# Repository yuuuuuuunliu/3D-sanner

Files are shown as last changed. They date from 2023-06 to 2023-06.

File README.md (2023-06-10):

# Ultrasonic 3D Scanner

This guide outlines the development process of our ultrasonic 3D scanner. We will provide resources in this repository that can be used to reproduce the project, as well as data for evaluating the accuracy of the measurement results. The ultrasonic 3D scanner utilizes ultrasound ranging to scan real-world objects, capturing the coordinates of various points on their surfaces. By processing the collected data, the scanner generates a three-dimensional model of the object, enabling an accurate digital representation of the object's size and dimensions. This technology holds immense potential for various applications, including but not limited to artifact preservation, educational applications, and reverse engineering. Our project specifically focuses on constructing a low-cost 3D scanner, aiming to make this technology more accessible for everyday use. By providing an affordable solution, we aim to promote the widespread adoption of this technology in everyday life.

Access our project presentation through this link: 

https://docs.google.com/presentation/d/14-DhOLEjQ7N0TpDgxVi51gBwk0Xk7jdvzFTlWsp83JA/edit?usp=sharing

We hope you enjoy exploring this guide and find it helpful in creating your own 3D scanner.
 
## Table of Contents
* [Description](https://github.com/yuuuuuuunliu/3D-sanner#Description)
* [List of Components](https://github.com/yuuuuuuunliu/3D-sanner#List_of_Components)
* [Method](https://github.com/yuuuuuuunliu/3D-sanner#Method)
* [Construction](https://github.com/yuuuuuuunliu/3D-sanner#Construction)
* [Product Review](https://github.com/yuuuuuuunliu/3D-sanner#Product_Review)
* [Future Development](https://github.com/yuuuuuuunliu/3D-sanner#Future_Development)
* [Contributors](https://github.com/yuuuuuuunliu/3D-sanner#Contributors)
* [Acknowledgments](https://github.com/yuuuuuuunliu/3D-sanner#Acknowledgments)

## Description
The ultrasonic 3D scanning device consists of two main components: a fixed ultrasonic distance sensor and a rotatable lifting platform. The ultrasonic distance sensor utilizes the reflection of sound waves to determine the distances between its position and various points on an object. The lifting platform is powered by a stepper motor and is driven by gears and screws to rotate and elevate the object. As the platform rotates, the object passes through the ultrasonic distance sensor in a spiral path, and the coordinates of the object's points are recorded.

Subsequently, we process the collected data using MATLAB and extract the outer contour of the scanned object to generate a three-dimensional model. This is achieved through an interactive program that allows us to visualize the reconstructed 3D model based on the acquired data.

## List of Components
  * Ultrasonic Distance Sensor - HC-SR04
  * Arduino Nano 3.x
  * 4 Phase ULN2003 Stepper Motor Driver PCB
  * 28BYJ-48 - 5V Stepper Motor
  * Arduino Uno Mini LE - MCU 8-Bit Embedded Evaluation Board
  * Screw and nut
  * PCB Board
  * Jumper wires
  * 3D-printed parts

## Method
We use HC-SR04 as the ultrasound distance sensor component.
  
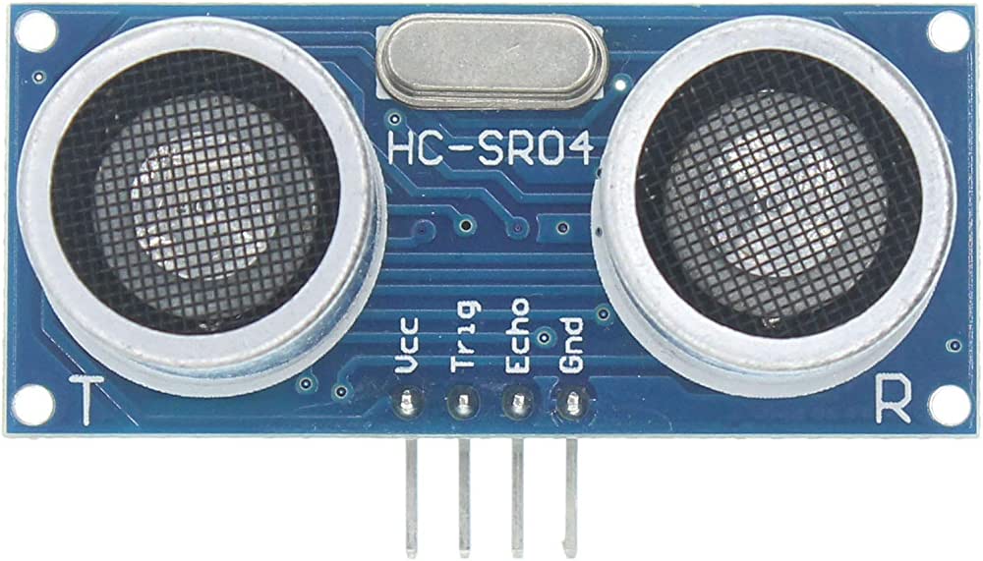
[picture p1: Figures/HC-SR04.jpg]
A picture of the distance sensor we used
  
  
The HC-SR04 module consists of four pins. The Vcc pin and GND pin are connected to the 5V and GND pins of the Arduino Nano, respectively. These pins serve as both power supply and logic level control (high/low). The Trig pin is an input pin of the HC-SR04 and is connected to the D3 pin of the Arduino Nano. The Echo pin is an output pin of the HC-SR04 and is connected to the D2 pin of the Arduino Nano. In fact, the Trig and Echo pins can be connected to any two digital I/O pins of the Arduino Nano. The HC-SR04 module consists of two piezoelectric transducers, one acting as a transmitter (marked with "T") and the other as a receiver (marked with "R"). 

To initiate a distance measurement with the HC-SR04 module, a voltage pulse is sent to the Trig pin. This voltage pulse is transformed into a sine wave by a local oscillator, and the resulting sine-shaped voltage signal is sent to the transmitter. The transmitter converts this voltage signal into a sound signal, emitting an 8-cycle sonic burst in the forward direction. Simultaneously, the receiver is set to a high state, and a timer starts counting. The emitted sonic burst travels through space and reflects when it encounters the nearest object. Upon receiving the reflected wave, the receiver changes to a low state, indicating the detection of the reflected signal, and the timer stops counting. 

The duration for which the receiver stays in a high state is equal to the time it takes for the sound to travel in space. Therefore, the distance between the sensor and the object can be calculated using the formula: d = (v * t) / 2, where t represents the measured time and v represents the speed of sound. The speed of sound is typically considered to be around 340 m/s, but it can vary depending on the medium and temperature conditions.

We aim to have three spatial dimensions for each data point to determine their coordinates in space accurately. Since the trajectory of the object moving in front of the sensor is spiral-shaped, expressing the coordinates in cylindrical coordinates would be the most convenient way. The actual measurement results include two dimensions - time (t) and distance (d). By introducing the angular velocity (ω) of the rotating disc and the vertical velocity (v), we can represent the angle (θ) between the point's position along the radial axis and the initial radial axis as a function of time (t), as well as the distance (z) between the point's position and the initial plane as a function of time (t). Introducing the distance (r_max) from the sensor to the vertical axis of the cylinder allows us to calculate the distance (s) between the measurement point and the vertical axis of the cylinder. Hence, we can determine the cylindrical coordinates (s, θ, z) of each point on the object's surface in a coordinate system with the initial plane as the xy-plane and the vertical axis of the cylinder as the z-axis. The specific formulas for the calculations are as follows:

$$s = r_{max} - d$$

$$\theta = \omega * t$$

$$z = v * t$$

Once we have marked all the points on the object's surface in space, our goal is to construct the outer surface of the object using these points. While we can easily visualize the outer surface, computers have numerous possibilities for constructing planes based on the given points. Therefore, we need to specify the desired planes. The instruction we provide to the computer is to connect points with adjacent θ and z values, and to fill all the quadrilaterals bounded by the connecting lines. This process allows us to construct the outer surface of the object. 

For the specific MATLAB graphing code, please refer to the following location, where I generate data for simulation purposes:https://github.com/yuuuuuuunliu/3D-sanner/blob/main/graph.mlx

The expected outcome is shown below:

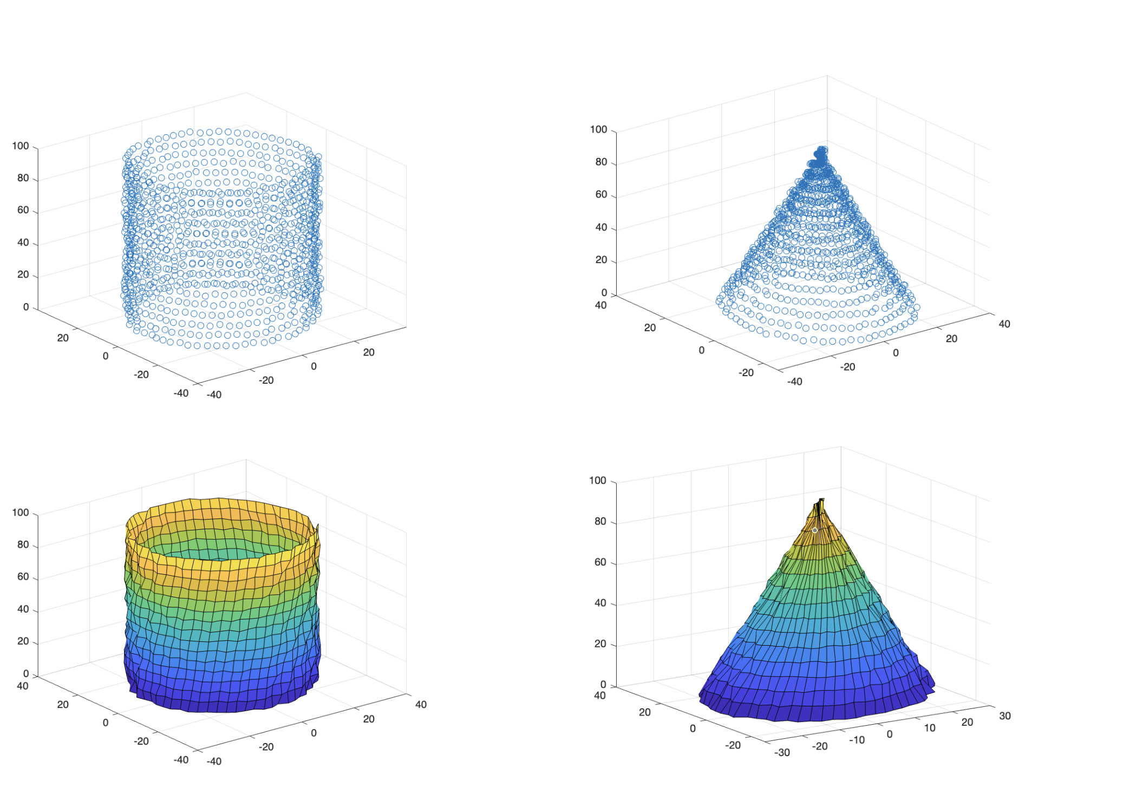
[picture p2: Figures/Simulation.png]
Outer surface of a cylinder and a cone using simulated data
  

In order to scan the 3D information of an object, we rotate the object and make it move upward. The sensor is fixed and gets information when the system is start to work. In this way, we just need to collect the information on time and distance from the sensor to the object. The location can be calculated from the time and velocity of the step motor. The step motor rotates one lap in 4 seconds. The plate rotates 1 lap using 10 seconds. In each lap, the object will raise 2 mm with the average speed with the plate. 

The rotating frame is motivated by a stepper motor with following circuit connection:

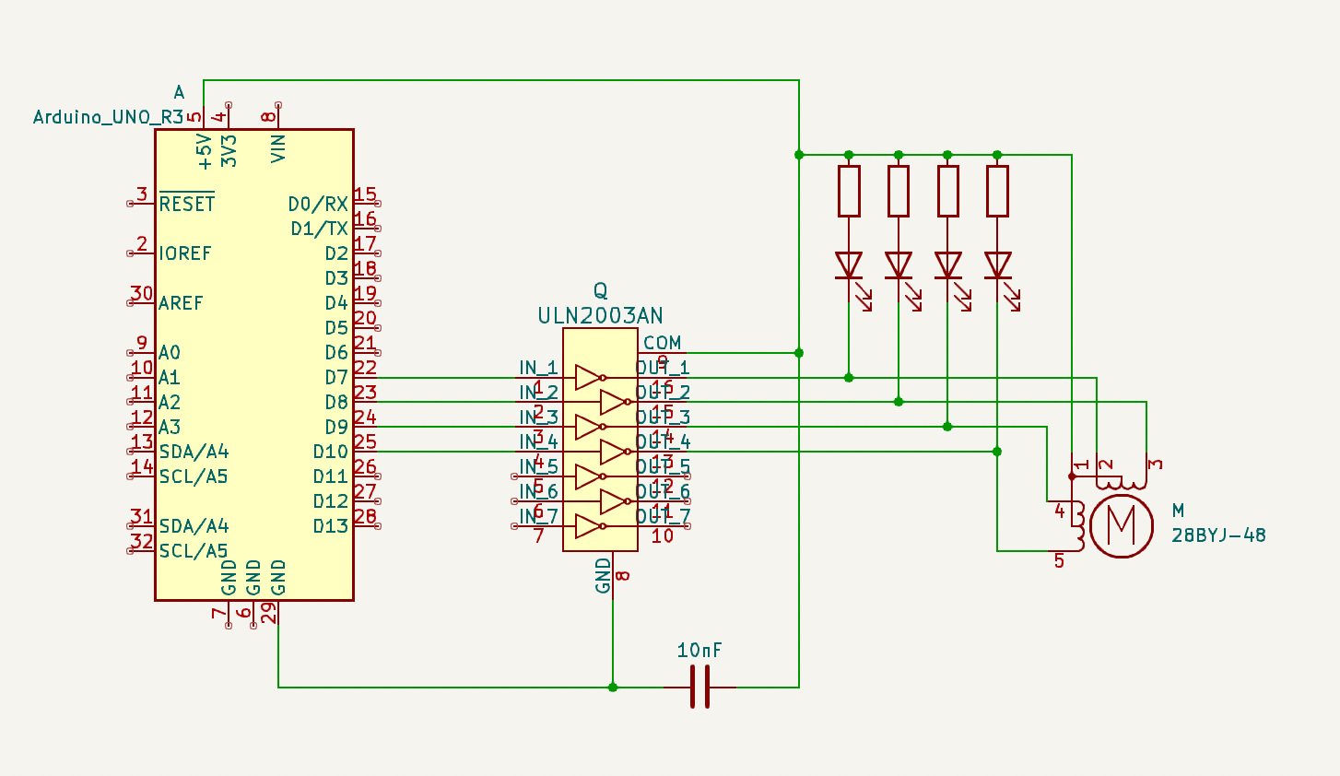
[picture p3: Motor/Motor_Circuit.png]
Circuit connection of stepper motor, driver, and Aduino
  

## Construction

Before scanning the object, we build up a frame to hold all components. For most of the components, we used 3D Modeling to create and then print them out with 3D printers. All of STL. Files can find in the folder of [Frame](https://github.com/yuuuuuuunliu/3D-sanner/tree/main/Frame). Some components have different versions, we did lots of improvements for every component. 

The plate will hold the object we are going to scan. The main frame is going to fix the nut and hold the whole system. It can replace by box instead of 3D printing components, because large 3D printing components take a long time, which may take up to several days. A strew is connect with the plate and the strew gear. Before assemble them, the nut and connection should install first. From the top to the bottom of the strew, the sequence should be plate, nut, connection, and strew gear. The step motor should connect to the middle whole of the connection. Then, install step motor gear onto it and check the connection between step motor gear and the strew gear. The connection is free to rotate with the strew. The frame should limit this rotation and make sure it can move up and downward with the strew. Other parts work for fix the sensor, they are flexible to do adjustments due to your different use. 

* [Different printers may print out components with different uncertainty. Some adjustments may be needed especially for the gears. If the gears have spinning conditions, enlarging the teeth of gears for 1mm is a good choice.] 

HC-SR04 has a range from 2cm to 4m. Experimental results have shown that the HC-SR04 distance sensor has a measurement standard deviation of less than 0.5mm. The difference between measured values and actual values is typically less than 2cm, with the majority of errors staying below 0.5cm. Therefore, we can consider the HC-SR04 to be a precise and accurate distance sensor. Additionally, due to its stable numeric uncertainty rather than percentage uncertainty, we can reduce errors by applying it to large objects. This improvement strategy will be further discussed in the future development section.

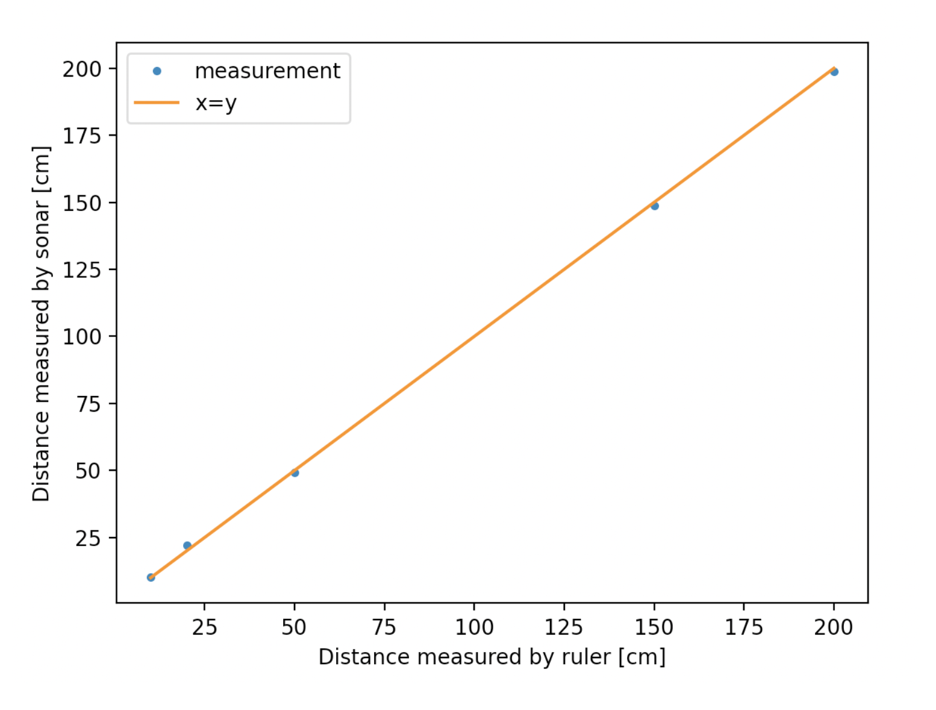
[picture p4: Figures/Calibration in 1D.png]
A plot of the sensor's measurements against the actual length
  

The distance sensor we utilize emits a conical wave with a raypath angle of 15 degrees. This angle allows the sensor to be sensitive to a wider area. However, in situations where high precision distance measurements are required, such high sensitivity can lead to unnecessary feedback. To mitigate this, we can place a rough absorbent block beneath the sensor. This block, with its rough surface, causes non-radial sound waves to undergo multiple reflections in a short period of time, dissipating a significant amount of energy and effectively absorbing unwanted reflected waves. 

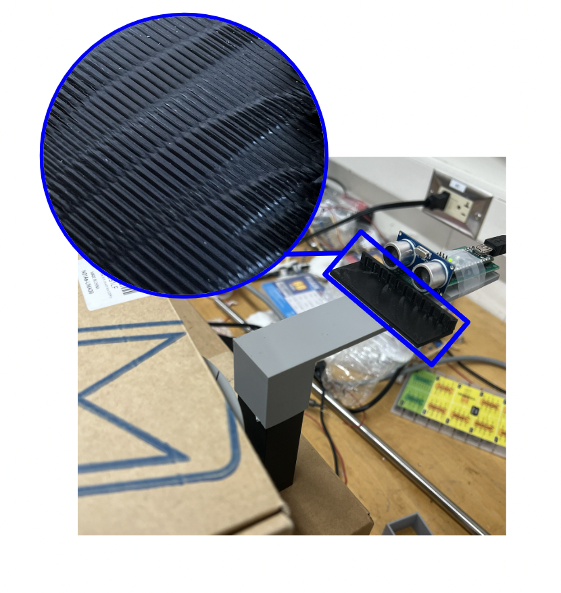
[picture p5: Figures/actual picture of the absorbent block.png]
A picture of the absorbent block and a close-up look of its surface
  

The figure below illustrates the results obtained when using the sensor to measure a stationary object (i.e., where the distance from the point to the origin, s, remains constant), and processing the data using MATLAB to generate a three-dimensional image in cylindrical coordinates. It is evident that the erroneous refracted points have been effectively eliminated through the use of the absorbent block.
 
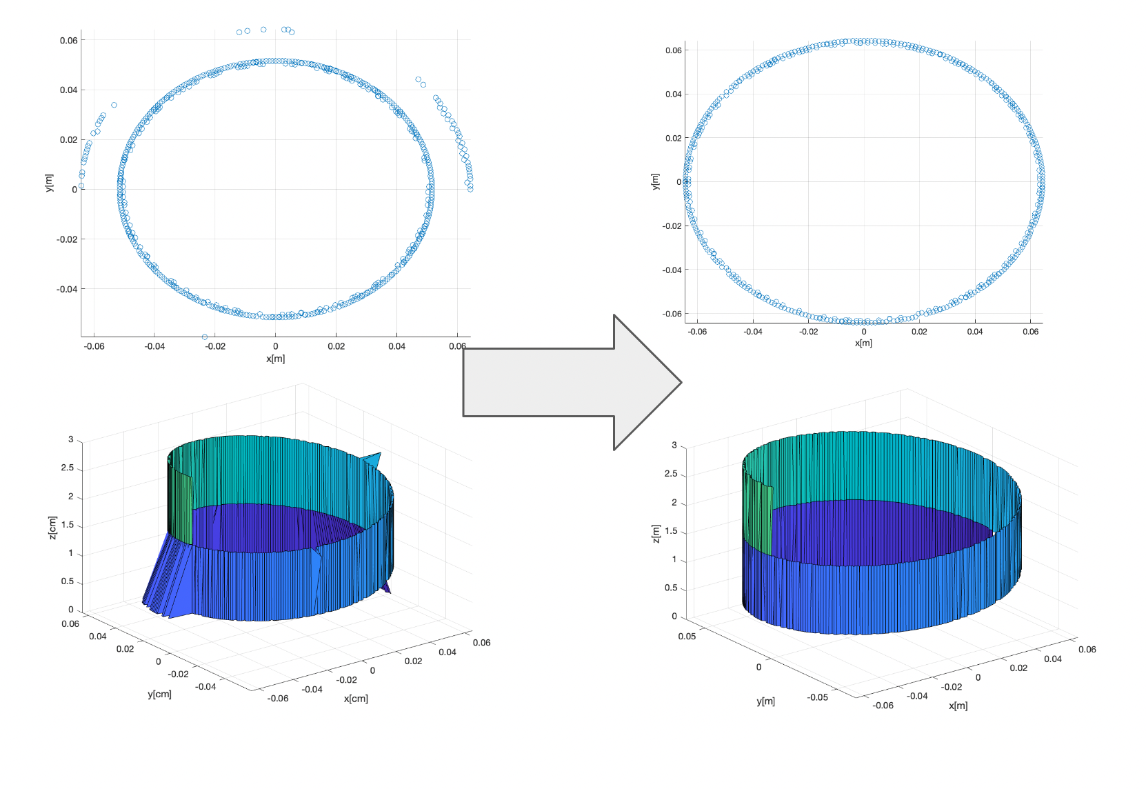
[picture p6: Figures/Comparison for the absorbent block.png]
Comparison of plots before and after using the absorbent block
  
  
We use the device to scan the surface of a cylindrical object. Ideally, the results obtained after the rotation of the turntable should be similar to the results obtained when the turntable is stationary, as the object exhibits cylindrical symmetry around the z-axis. However, in reality, the results obtained after the rotation of the turntable exhibit significant fluctuations. By observing the raw data and examining the scanned image of the object's outer surface based on the measurement results, we notice that the fluctuations in the raw data appear to be periodic. This observation is further supported by the presence of a wavy surface in the 3D representation. Therefore, we have decided to use the "smoothdata" function in MATLAB to remove these fluctuations.

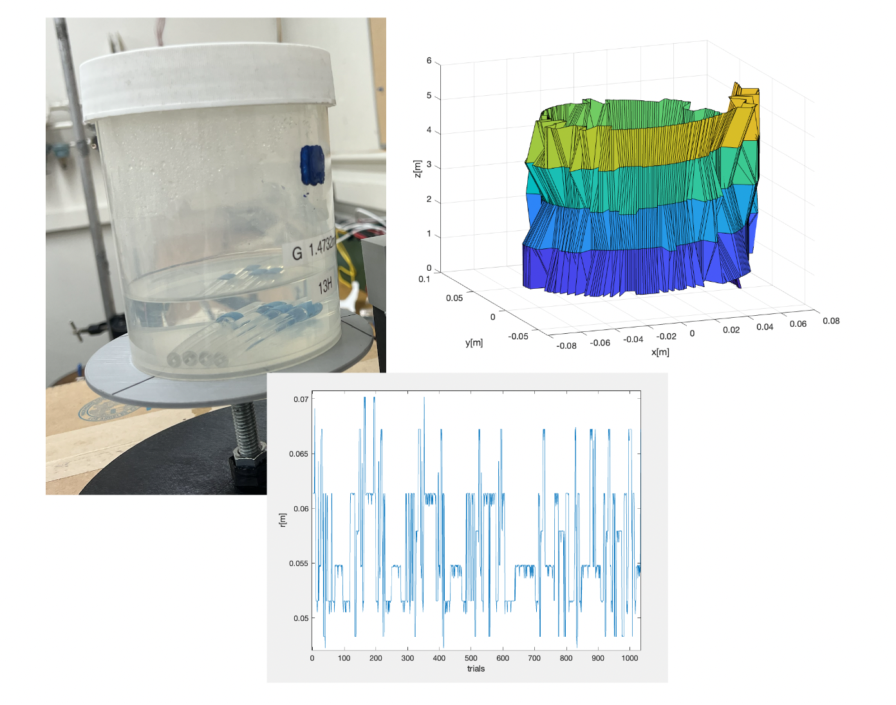
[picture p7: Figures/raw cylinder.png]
Pictures that showcase the cylindrical object, the raw data of r over multiple trials, and a 3D graph generated based on the measurements
  

The code we used is as follows:

```
smoothdData = smoothdata(r, "movmean", 50)
```

In this code, "r" represents the data to be processed, "movmean" denotes the data processing method, and "50" indicates the window size. The provided function creates a moving window with a size of 50 data. This window calculates the average value of all 50 data it contains and treats it as the smoothed data. Then, the window shifts by one value and the process is repeated. The window moves along the data while continuously calculating the average value until all the data is smoothed. Plotting the graph using the smoothed data reveals that a significant amount of noise has been removed. The resulting image exhibits a relatively smooth surface, which is what we desired.

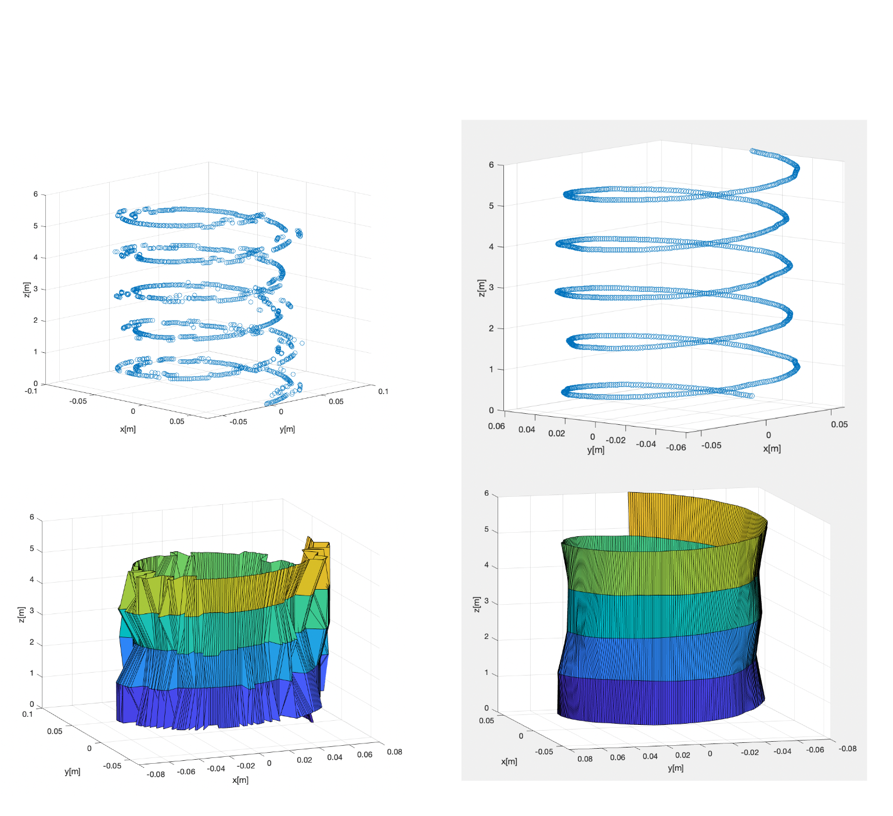
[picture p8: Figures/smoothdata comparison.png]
A comparison of the final 3D graphs between using the smoothdata() function and not using it
  

## Product Review

### Scanning two stacked cylinders with different radius

The arrangement of the scanned objects is illustrated in the following diagram:

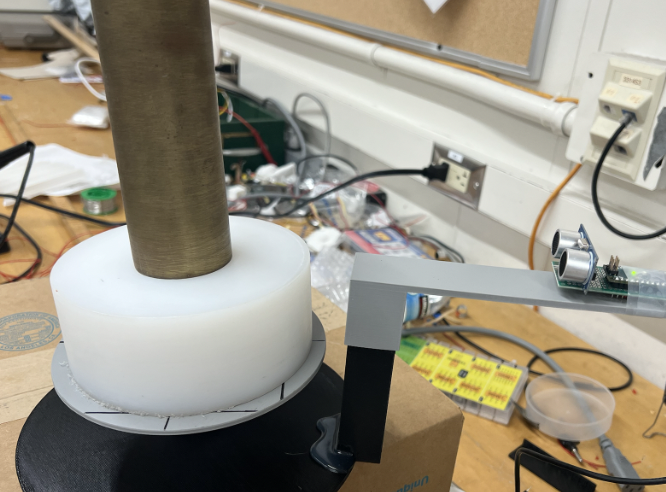
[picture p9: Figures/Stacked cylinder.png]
The arrangement of two stacked cylinders that will be scanned for review
  
 
The lower cylinder has a radius of approximately 6.5cm, while the upper cylinder has a radius of approximately 2.5cm. Both the raw data and smoothed data show a reduction in radius, which corresponds to our actual setup. 

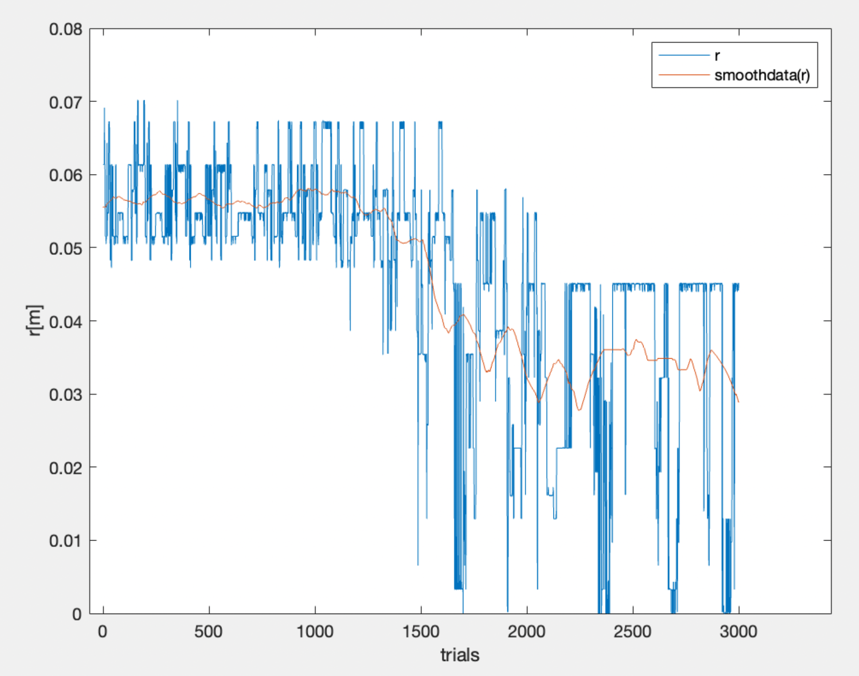
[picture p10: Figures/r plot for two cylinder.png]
The plot showing the variation of distance r over trial for both raw data and smoothed data
  

We then examine the processed 3D image. The image roughly depicts the outer contours of two cylinders with different radii. At the same time, we can approximately read the measured values of the two cylinder radii from the graph, which are approximately 3cm and 6cm. Comparing these values to the actual data, we find an error of approximately 0.5cm, which aligns with the expected deviation in the initial direct measurements of distance using the ultrasonic sensor. Therefore, we can conclude that the precision of our obtained results is close to the inherent precision limit of the HC-SR04 sensor. For the current setup, this is a satisfactory outcome. Indeed, it is noticeable that in the region where the two cylinders are joined, the graph does not exhibit sharp edges as we would expect in the real world. Instead, there is a curved and smooth transition between the surfaces of the cylinders. This result is attributed to the 15-degree raypath angle of the sound waves, as we discussed earlier, and the inclination of the platform. Possible solutions for this issue will be elaborated in detail in the future development section.

  The 3D surface graph generated by MATLAB as well as the distribution of measured data points in 3D space (top view)
  
However, the resulting image this time does not resemble a box in any way. Upon careful observation of the scanning process of the box and experimenting with different platform rotation speeds in Matlab, we have found that the failure in imaging the box is due to the instability of the platform rotation speed.

### Scanning a box

Then we proceed to scan the box as illustrated in the following image:

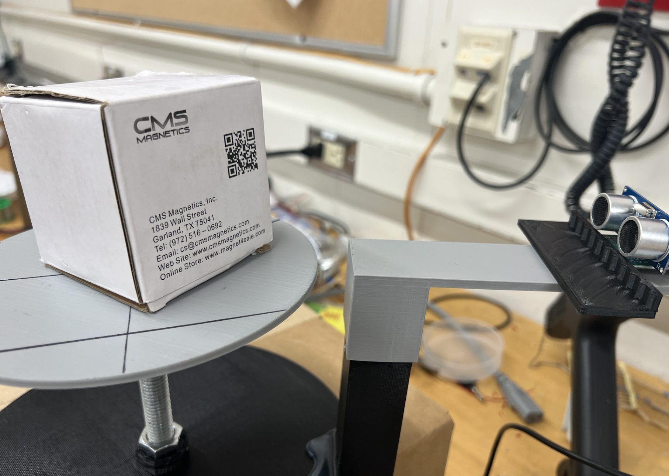
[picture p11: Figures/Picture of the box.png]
The picture of the box we will scan in this section
  
  
However, the resulting image this time does not resemble a box in any way. Upon careful observation of the scanning process of the box and experimenting with different platform rotation speeds in Matlab, we have found that the failure in imaging the box is due to the instability of the platform rotation speed. When processing the data in MATLAB to generate the 3D image, it assumes an ideal motion model for the platform based on a constant vertical speed and angular speed. However, during the actual measurement process, we observed that the platform's rotation speed is not stable. The time required for a point on the surface of the object to complete a full 2π rotation varies in each revolution. As a result, MATLAB can only ensure that the points on the same revolution as the set angular speed are in the right phase. However, MATLAB requires at least two revolutions of points to generate one complete surface. This discrepancy leads to the final generated result being distorted and skewed. We will provide a detailed explanation of the proposed solutions for this issue in the future development section.

  The 3D scan of the box in both scatter plot and surface plot versions

## Future Development
We have already mentioned some of the issues and unexpected results encountered in the previous discussion. In order to address these problems, we plan to upgrade the project in the future. Additionally, we will conduct corresponding experiments to investigate the causes of the unexpected results. Specific future measures that can be undertaken are outlined as follows:

### Upgrade of the rotating platform

At the current stage, the rotating platform exhibits the following issues: Firstly, the rotating disc is not perfectly horizontal, causing a precession in the coordinate system in which the object is located as perceived by the distance sensor. Secondly, there are certain issues with the gear size, resulting in improper engagement. The gears that rotate synchronously with the rotating disc often experience slipping and jamming, leading to an unstable rotational speed. Lastly, the device is built on a cardboard box, which has low density. This causes the entire setup to shake under the influence of the stepper motor driving and the inertia of object rotation, significantly affecting the final scanning results. This shaking may also be a potential cause of the periodic noise observed in the raw data we discussed earlier，although further measurement and analysis are required to confirm this hypothesis.
Adjustments on 3D printing can solve some problem. For example, adjust the size of plate and enlarge the teeth of gears can solve the first two problems. Also, this method can make the system works more stable as well, which can reduce some vibration. Also, the frame should be upgrade to all-3D-printed one. It may take a long time to print, but it is heavier and more stable. Additionally, create new 3D modeling of protection cover for the sensor may help to reduce noise. 

### Upgrade of the ultrasonic distance sensor

As mentioned earlier, the HC-SR04 sensor emits ultrasonic waves in the form of a cone with a vertex angle of 15 degrees. This characteristic introduces certain measurement errors and inaccuracies in capturing sharp edges of objects. We aim to narrow down the scanning range by utilizing phased array technology. Inspired by the video shared (https://www.youtube.com/watch?v=Evao3XUUAOY), we came up with the idea of employing a phased array approach to achieve this goal.By strategically spacing multiple wave sources and adjusting their phases, we can control the interference pattern of the emitted waves. This allows us to constructively interfere the waves along the desired path, forming a stronger sound ray, while causing destructive interference in other directions to minimize their impact on the main beam. We can build our own multi-wave source distance sensor to achieve a more focused detection beam. By using basic electronic components, we can design a distance sensor that provides analog signals instead of the digital output of the HC-SR04 module. By processing and analyzing the analog signals, we can extract information about multiple reflections, allowing us to obtain insights into the internal structure of objects.

### Upgrade of smoothdata() method

In the previous experiments, I chose a window size of 50 based on multiple trial runs. This particular window size was found to strike a balance between data accuracy and precision while avoiding potential trial-specific outcomes. However, upon realizing that the noise we want to eliminate is periodic, measuring the period of the noise will help us determine a more appropriate window size. Therefore, in the future, we will attempt to measure the periodicity of the noise and explore the relationship between window size, periodicity of the noise, and the accuracy and precision of the final results by scanning objects with different shapes and symmetries.

### Research on periodic noise

Ideally, when scanning a cylindrical object with a base radius of R, the results should be consistent whether the turntable is rotating or stationary because both measurement methods essentially involve continuously measuring R. However, in reality, we have observed that when the turntable is stationary, the measurement error generated by the ultrasonic sensor is negligible. However, when the turntable starts rotating, significant periodic errors occur in the measurement results from the ultrasonic sensor, which can significantly impact the quality of the imaging. Therefore, we have developed some initial hypotheses regarding the origin of this periodic error: it stems from the rotation of the turntable. We aim to investigate whether the periodicity of the error changes with variations in the rotational speed of the turntable. Through this experiment, we will have the opportunity to confirm the source of the error and conduct further research to pinpoint the underlying causes of the noise.

## Contributors

This project was undertaken as part of the PHYS 13CL course at UCSB.

We would like to extend our sincere appreciation to Professor Andrew Jayich and the teaching assistants, Robert Kwapisz and Eric Deck. Their unwavering support and guidance throughout these ten weeks have been invaluable to our project. We are also grateful to them for organizing enjoyable board game nights that helped alleviate our stress, and for feeding our restless souls with pizza and Fanta.

Furthermore, we would like to express our gratitude to thet group of Katelyn Saxen, Katya Osipova, and Eric Zhu for generously sharing their experiences and providing valuable insights when we encountered challenges during our progress.

Special thanks go to Raffi Shirinian for his assistance in utilizing the 3D printer and for lending us his personal hot glue gun, which greatly facilitated our project.

We would also like to thank Max Kolevski for his assistance in procuring the stepper motor and driver from ILG, which were instrumental to the success of our project.

Lastly, we want to acknowledge and thank Reuben Beeler for his thought-provoking questions during the presentation. His inquiries inspired us to reevaluate our criteria for evaluating the scan results.

## Acknowledgments
* [Datasheet of HC-SR04](https://cdn.sparkfun.com/datasheets/Sensors/Proximity/HCSR04.pdf)
* [Datasheet of 4 Phase ULN2003 Stepper Motor Driver PCB](https://www.electronicoscaldas.com/datasheet/ULN2003A-PCB.pdf)
* [Datasheet of 28BYJ-48 – 5V Stepper Motor](https://www.mouser.com/datasheet/2/758/stepd-01-data-sheet-1143075.pdf)
* [Control 28BYJ-48 Stepper Motor with ULN2003 Driver & Arduino](https://lastminuteengineers.com/28byj48-stepper-motor-arduino-tutorial/)
* [DIY Sonar Scanner Using Phased Array](https://www.youtube.com/watch?v=Evao3XUUAOY)

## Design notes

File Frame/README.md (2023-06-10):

## Frame
This component has two versions, it is mainly designed for holding and fixing all the needed components and parts for the project. Strew's nut should be fixed on it. 

## Gear
This is connnect to the step motor. It works to transmit force from step motor to the strew and then rotate the object. "gear, step motor v2" is the second version of it. The second version has longer teeth, which solve the problem of spinning between two gears. 

## Strew Gear
This is design to fix with the strew we bought. The step motor will transmit force through step motor gear to make the strew rotate. 

## Connection
This components is design to hold the step motor and connect strew with the step motor. This connection should move up or down with the strew and step motor as rotating, but it should not rotate with the strew. In this way, the step motor can generate the strew to move up and rotate. 

## Coverage Frame
This component is designed to hold our sensor. the rectangle part is use to connect with the frame. It is a seperate part from the frame because of the limited space for the 3D printer. 

## Rail Base
This is design for the 2-D experiment. It works with the step motor and generate the sensor to move in a straight line. 

## Plate
This object connects to the strew directly. It rotates with the strew and hold the object we are going to scan. 

### Attention
In order to connect different components will. I suggest to print the coverage frame with a 1mm-1.5mm larger width, the step motor gear with 1mm longer teeth. It is able to add more teeth for the strew gear. The original strew gear has 20 teeth which is 2.5 times teeth that the step motor gear has. The original one is more convenient for calculating the angular speed of plate.

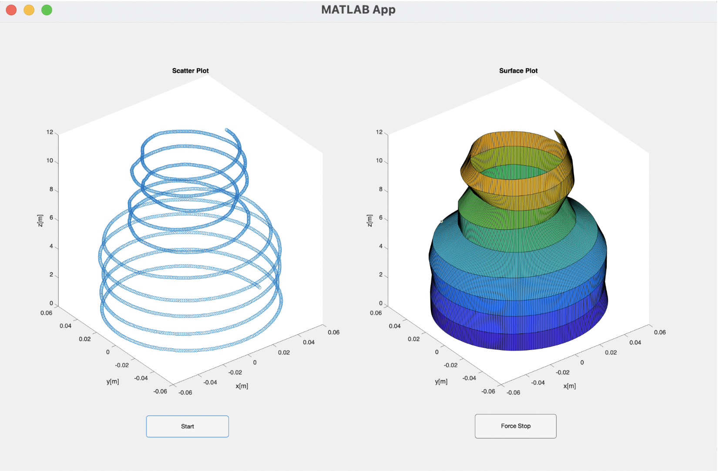
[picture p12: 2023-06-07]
Interface/interface.png

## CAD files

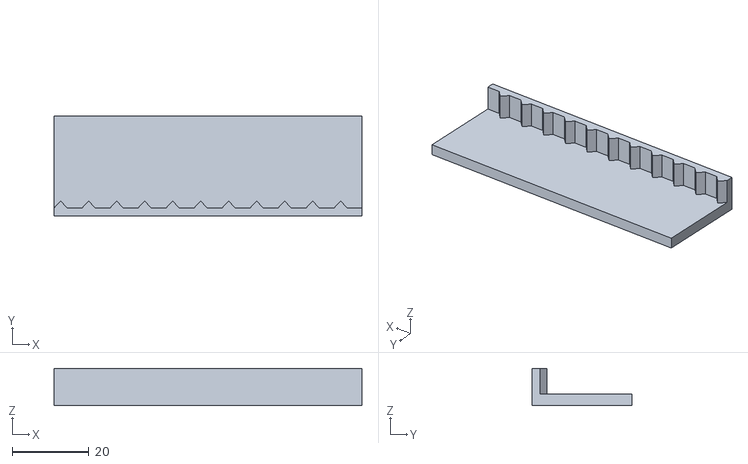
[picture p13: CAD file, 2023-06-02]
Frame/rail bas v1.stl
80.3 x 26.1 x 9.70

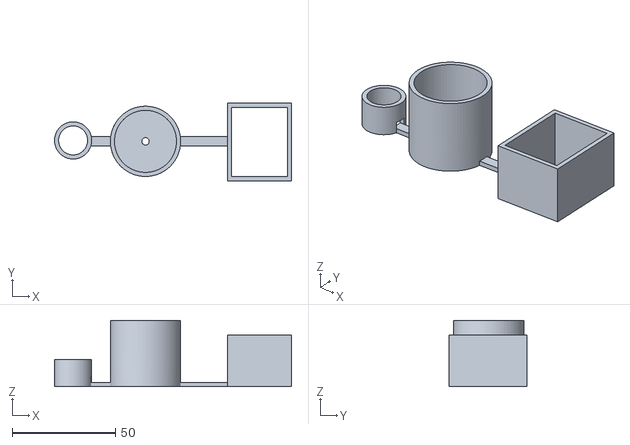
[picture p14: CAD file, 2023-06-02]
Frame/connection.stl
114.6 x 37.5 x 32.0

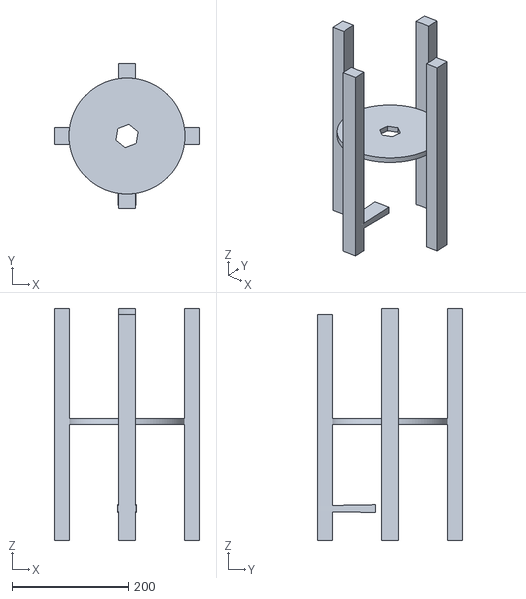
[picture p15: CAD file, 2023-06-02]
Frame/frame v2.stl
250.0 x 250.0 x 400.0

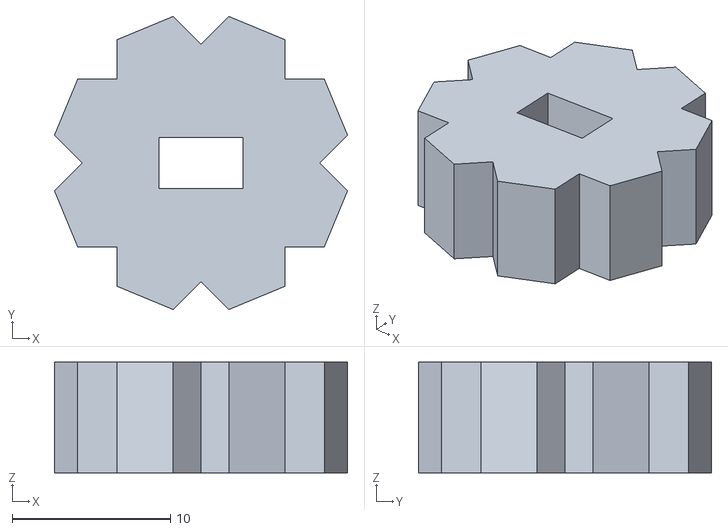
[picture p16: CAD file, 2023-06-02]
Frame/gear.stl
18.5 x 18.5 x 7.00

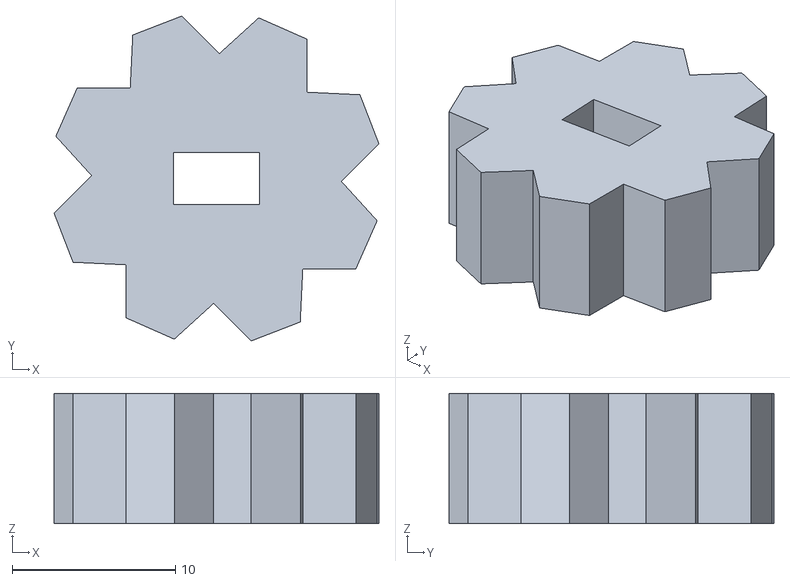
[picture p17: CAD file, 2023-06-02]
Frame/gear, step motor v2.stl
19.9 x 19.9 x 8.00

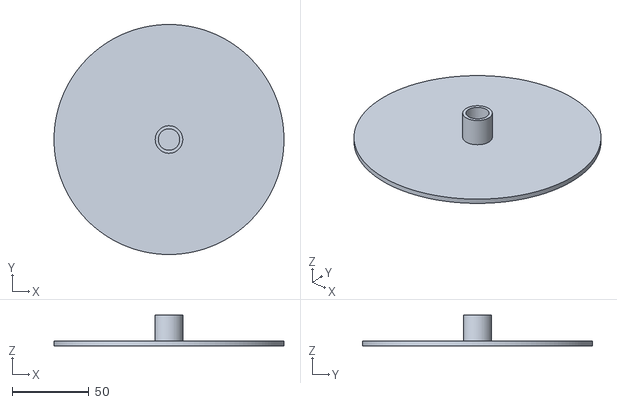
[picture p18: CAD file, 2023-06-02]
Frame/plate v1.stl
150.0 x 150.0 x 20.0

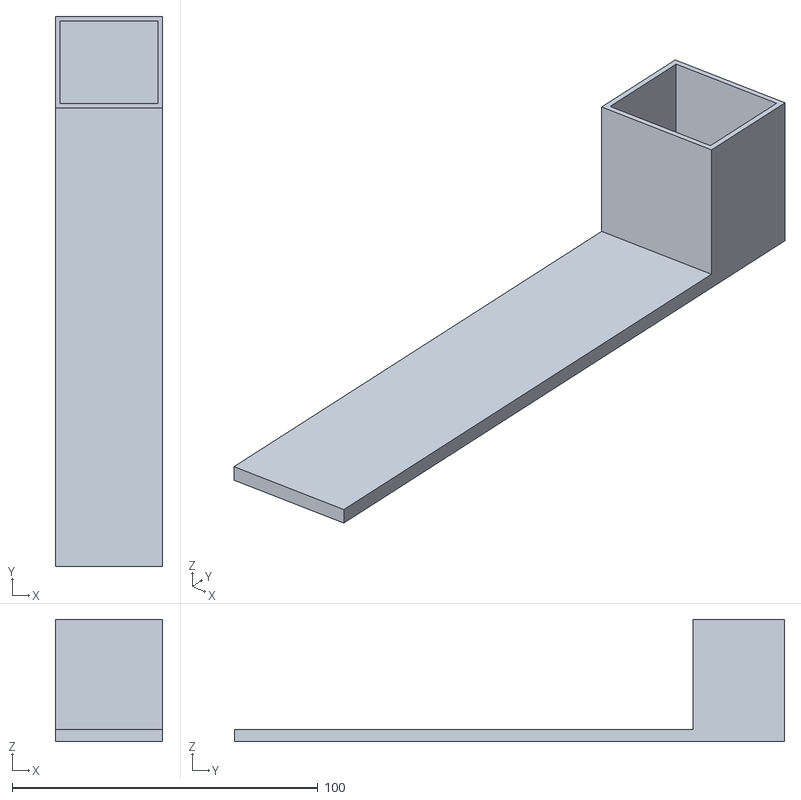
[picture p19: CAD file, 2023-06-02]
Frame/coverage frame.stl
35.0 x 180.0 x 40.0

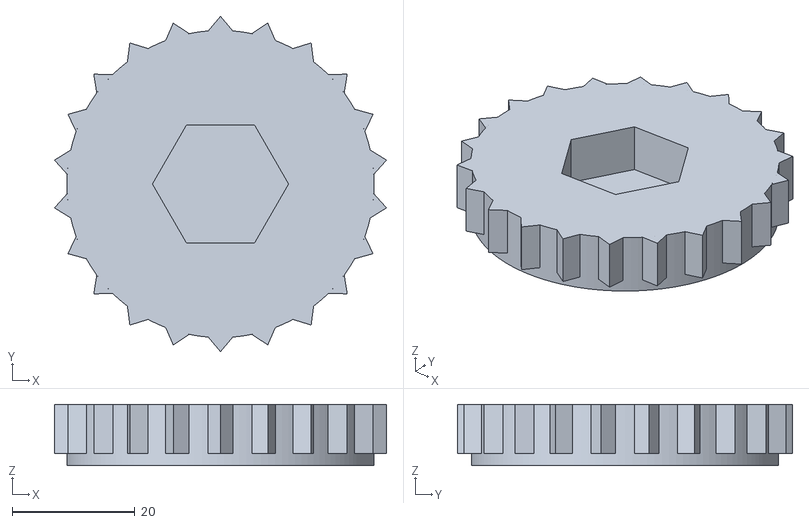
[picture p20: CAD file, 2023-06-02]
Frame/strew gear v2.stl
54.0 x 54.6 x 10.0

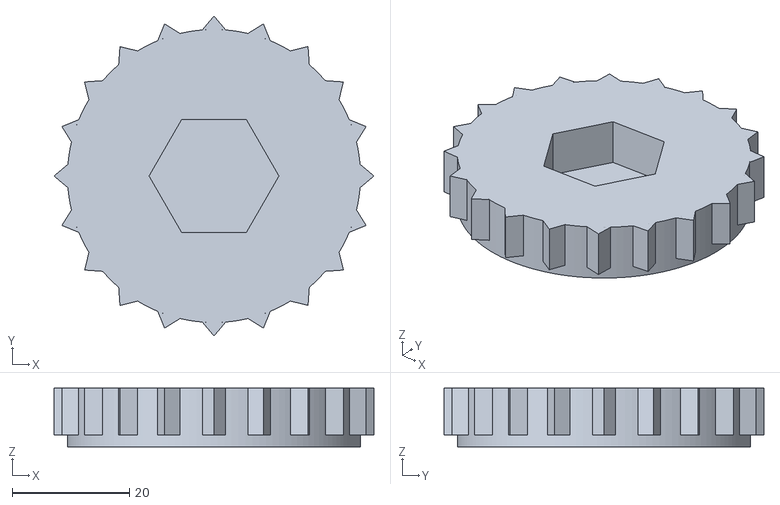
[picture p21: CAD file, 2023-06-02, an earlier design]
Frame/strew gear v1.stl
54.6 x 54.6 x 10.0

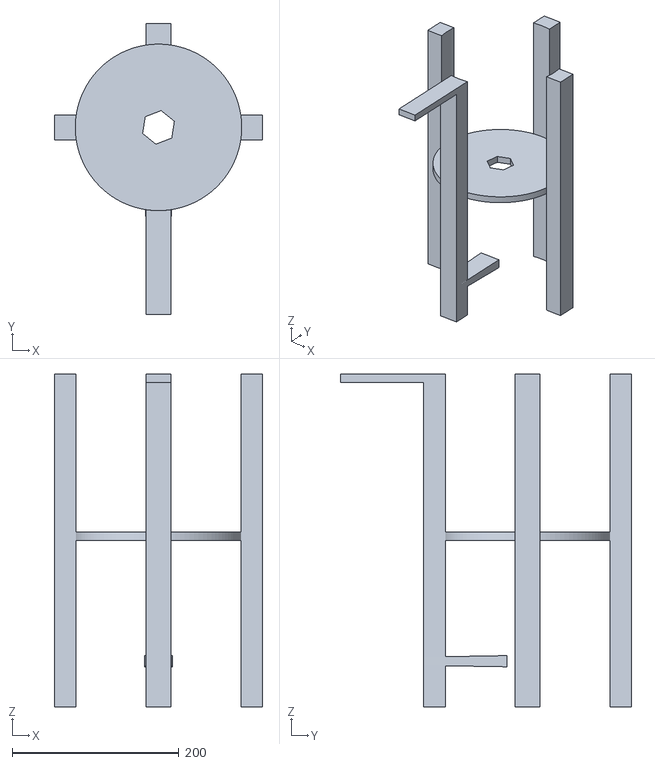
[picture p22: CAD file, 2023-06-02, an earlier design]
Frame/frame v1.stl
250.0 x 350.0 x 400.0

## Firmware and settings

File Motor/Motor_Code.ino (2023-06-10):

#include <Stepper.h>

const int stepsPerRevolution = 2038;

Stepper myStepper = Stepper(stepsPerRevolution, 8, 10, 9, 11); 
//Create a stepper object with its 4 pins connecting to D8, D10, D9, and D11 of Aduino Uno, respectivly

void setup() {
    //leave it blank
}

void loop() {
 while (true) {
  myStepper.setSpeed(15); //The speed of motor is set to 15 RPM
  myStepper.step(stepsPerRevolution); //Lowering the platform
  //myStepper.step(-stepsPerRevolution); //Raising the platform
  }
}
